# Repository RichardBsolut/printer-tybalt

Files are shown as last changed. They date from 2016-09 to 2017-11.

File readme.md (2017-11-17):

# Tybalt

my version of the [Printer Kitten](https://github.com/woolfepr/Printer-Kitten)

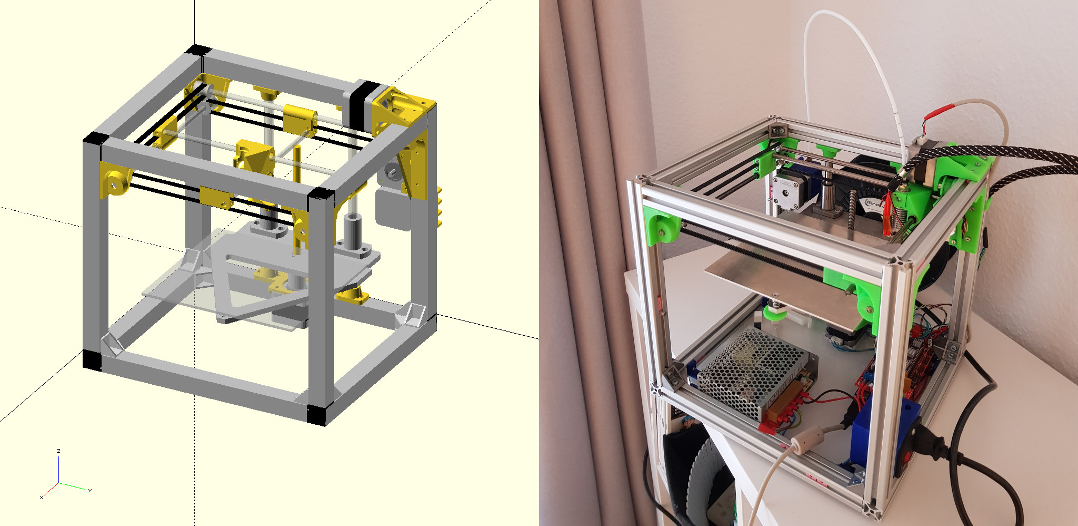
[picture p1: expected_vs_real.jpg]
Expected vs Real


### Why not simple use Kitten ?

Kitten only publishs the stl file, now we have openscad parts.
Mit 34mm schnupfmuffe und vorzerstaeuber druckluft trichter waere sehr schoen.

## Bom

The list is more an  overview not a final list

| Part | Amount | Price | Final Price | Comment
|---|---:|---:|---:|:---|
| Nema 17 | 4 | 2.65 € | 10.60 € | Lucky ebay shot |
| Power Supply 12V-/4,2A | 1 | 14.35 € | 14.35 € | [Pollin](http://www.pollin.de/shop/dt/OTc4ODQ2OTk-/Stromversorgung/Netzgeraete/Festspannungs_Netzgeraete/Schaltnetzteil_MEANWELL_RS_50_12_12_V_4_2_A.html) |
| Power plug | 1 |  6.00 € | 6.00 € | [Amazon](https://www.amazon.de/dp/B00ZCMOIYA) |
| Hot end | 1 | 8.69 € | 8.69 € | [Amazon](https://www.amazon.de/dp/B00V5W00RU) |
| Fan 12V 25x25x10mm | 1 | 3.90 € | 3.90 € | [Reichelt](http://www.reichelt.de/FAN-2510-12V/3/index.html?ACTION=3&LA=446&ARTICLE=11003&artnr=FAN-2510+12V) |
| Ramps + Arduino Mega + Motor Driver | 1 | 15.24 € | 15.24 € | [Aliexpress](https://de.aliexpress.com/item/Mega-2560-R3-1pcs-RAMPS-1-4-Controller-5pcs-A4988-Stepper-Driver-Module-for-3D-Printer/1227994962.html)
| Hallsensor TLE 4905L | 3 | 0.64 € | 1.92 € | [Reichelt](http://www.reichelt.de/TLE-4905L/3/index.html?ARTICLE=25717)
| GT2 Pulley 16  | 2 | 1.00 € | 2.00 € | [Ebay](http://www.ebay.de/itm/181838550531)
| GT2 Pulley 20  | 8 |  | 5.60 € | [Aliexpress](https://www.aliexpress.com/item/Hot-Sale-10pcs-lot-3D-Printer-Parts-Accessory-GT2-20teeth-20-teeth-Timing-Alumium-Pulley-Bore/32323132171.html)
| GT2 Belt  | 3 meter | 1.00 €  | 3.00 € | [Ebay](http://www.ebay.de/itm/161918795821)
| Bearing 626ZZ  | 8 | 0.75 €  | 6.00 € | [Pollin](http://www.pollin.de/shop/dt/ODY1OTU1OTk-/Werkstatt/Eisenwaren/Lager/Kugellager_626ZZ.html)
| Linear shaft D 10mm L 230mm | 2 | 6.61 €  | 13.22 € | [Misumi](http://www.misumi-europe.com/de/e-catalog/vona2/detail/110302634310/)
| Linear Bushing LHICD10 | 2 | 10.98 €  | 21.96 € | [Misumi](http://www.misumi-europe.com/de/catalog/vona2/detail/110300026970/)
| Linear Bushing LMKW6 | 2 | 7.20 €  | 14.40 € | [Misumi](http://www.misumi-europe.com/de/catalog/vona2/detail/110302037730/)
| Stripper Bolt MSB5-20 | 2 | 0.60 €  | 1.20 € | [Misumi](http://www.misumi-europe.com/de/catalog/vona2/detail/110300249140/)
| Lead Screw THSL-200-8D 200m | 1 | 5.87 € | 5.87 € | [Aliexpress](https://de.aliexpress.com/item/3D-Printer-THSL-200-8D-Lead-Screw-Dia-8MM-Pitch-2mm-Lead-4mm-Length-200mm-with/32702416900.html)
| **Frame** |
| 20x20 I-Typ Nut 5 L: 250mm | 10 | 0.73 € | 7.30 € | [motedis](http://www.motedis.com/shop/Nutprofil/20-I-Typ-Nut-5/Aluprofil-20x20-I-Typ-Nut-5::1076.html) |
| 20x20 I-Typ Nut 5 L: 210mm | 2 | 0.62 € | 1.24 € | [motedis](http://www.motedis.com/shop/Nutprofil/20-I-Typ-Nut-5/Aluprofil-20x20-I-Typ-Nut-5::1076.html) |
| Winkel 20 I-Typ Nut 5 | 16 |  | 12.57 € | [motedis](http://www.motedis.com/shop/Nutprofil-Zubehoer/Zubehoer-20-I-Typ-Nut-5/Winkel-20-I-Typ-Nut-5::732.html) |
| M3 Screws | a lot | | |
| **Heated bed** |
| Heated bed 12x12cm 230V 110 Watt | 1 | 25.00 € | 25.00 € | [Ebay](http://www.ebay.de/itm/322240833571) |
| SSR-40DA | 1 |  4.21 € | 4.21 € | [Amazon](https://www.amazon.de/dp/B008OF0PBC) |
| ***Total*** | | | ***184.27 €*** | + unbelievable amount of postage |

## Printed parts
| Part | Time | Length | Gram |
|---|---:|---:|---:|
| **Carraige** |
| Clamps | 25m | 1.62m | 5g |
| Carriage | 1h 55m | 9.19m | 24g |
| **Motor** |
| y | 50m | 4.07m | 12g |
| x | 1h 35m | 7.94m | 24g |
| z | 41m | 3.31m | 10g |
| Beltguide | 1.7m | 1.31m | 4g |
| **Frame** |
| Z Hold | 53m | 3.99m | 12g |
| Z Magenet | 10m | 0.53m | 2g |
| **Printhead** |
| Printhead | 1h 30m | 6.96m | 21g |
||
| ***Total*** | *8h 16m* | *39.31m* | 114g |

*Finally*
http://pr0gramm.com/top/1498986

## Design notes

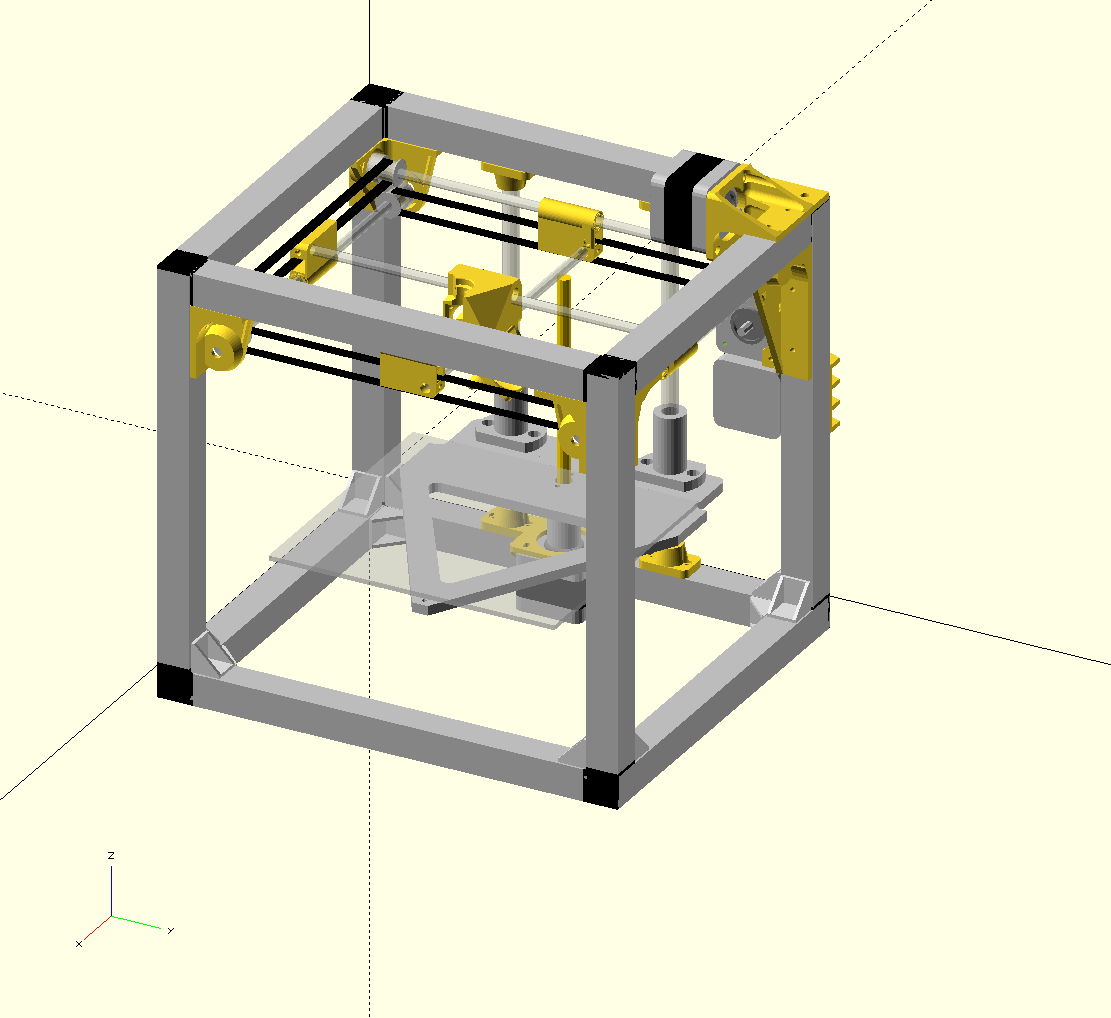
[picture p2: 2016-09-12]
expected.png

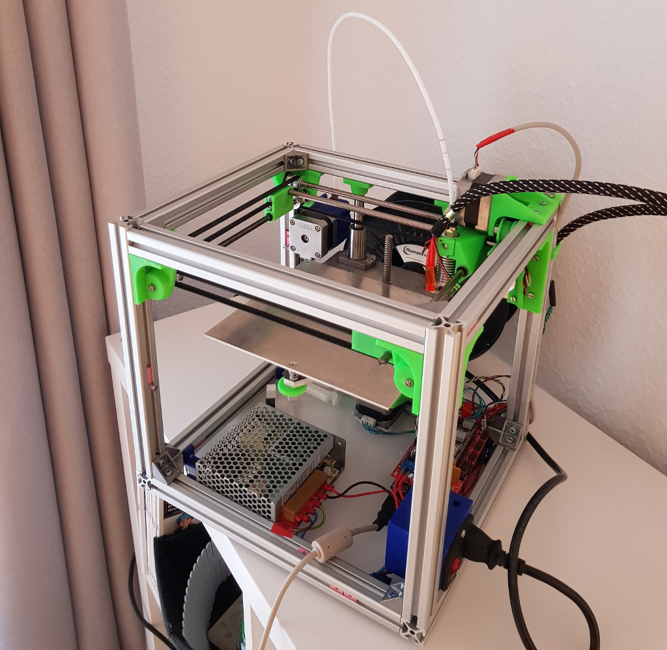
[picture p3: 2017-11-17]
real.jpg

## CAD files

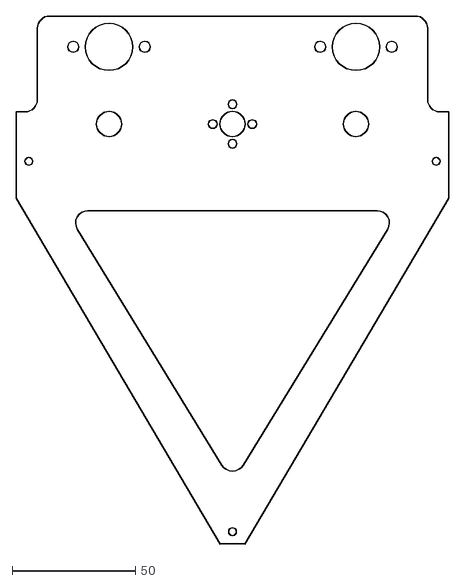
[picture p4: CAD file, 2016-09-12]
dxf/traegerplatte.dxf
175.0 x 213.9

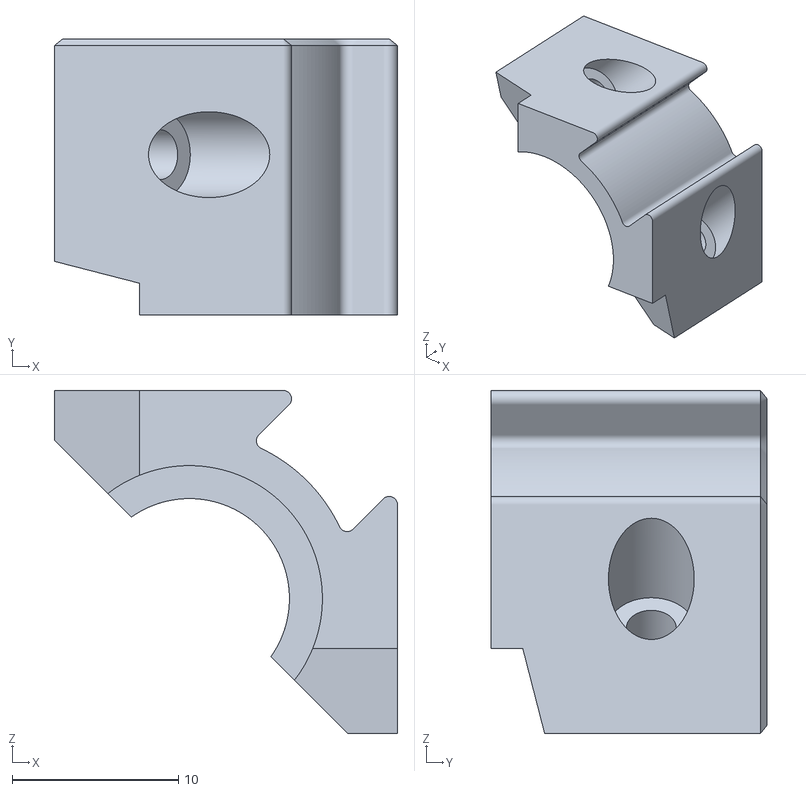
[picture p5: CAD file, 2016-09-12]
kitten_parts/print_head_clamp.stl
20.6 x 16.6 x 20.6

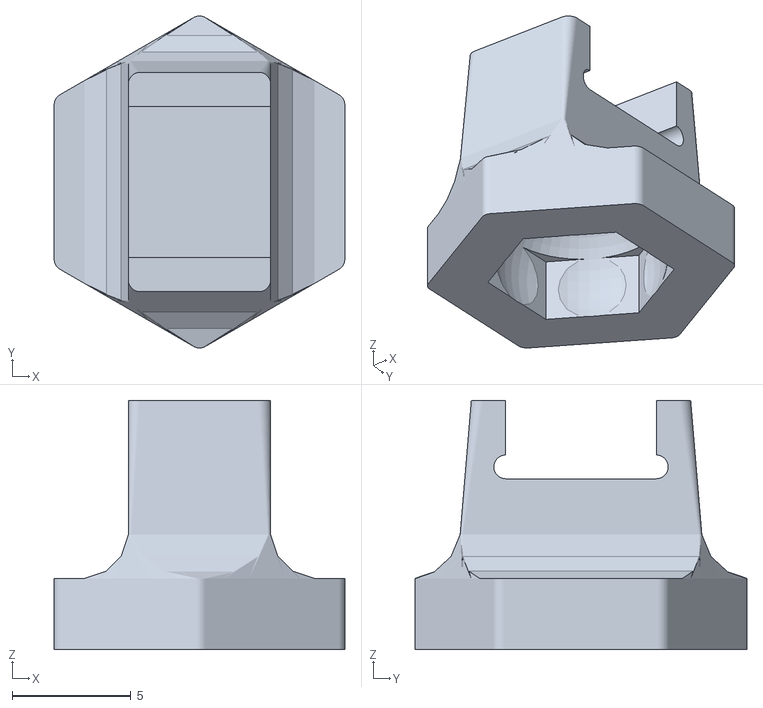
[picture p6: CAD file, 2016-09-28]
output/simple_zprobe.stl
12.3 x 14.0 x 10.5

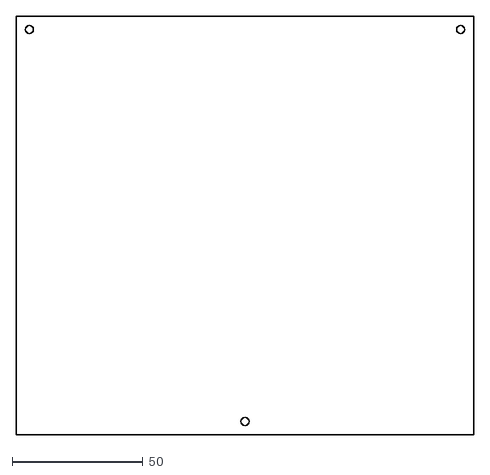
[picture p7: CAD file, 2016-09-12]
dxf/platte.dxf
175.0 x 160.0

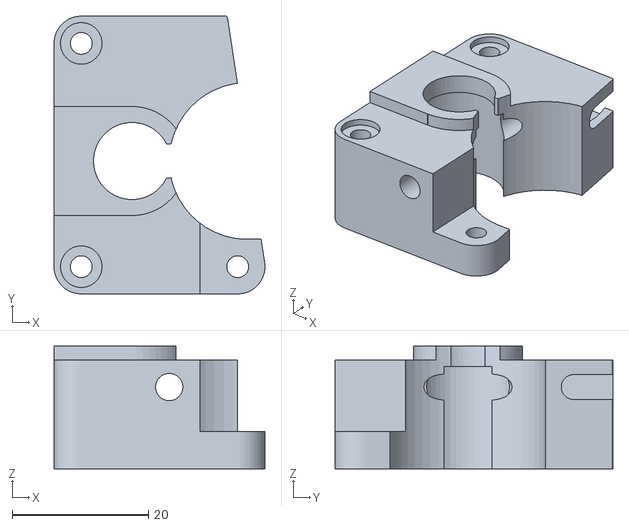
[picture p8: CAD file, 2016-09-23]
output/extruda2_base.stl
30.9 x 40.7 x 18.0

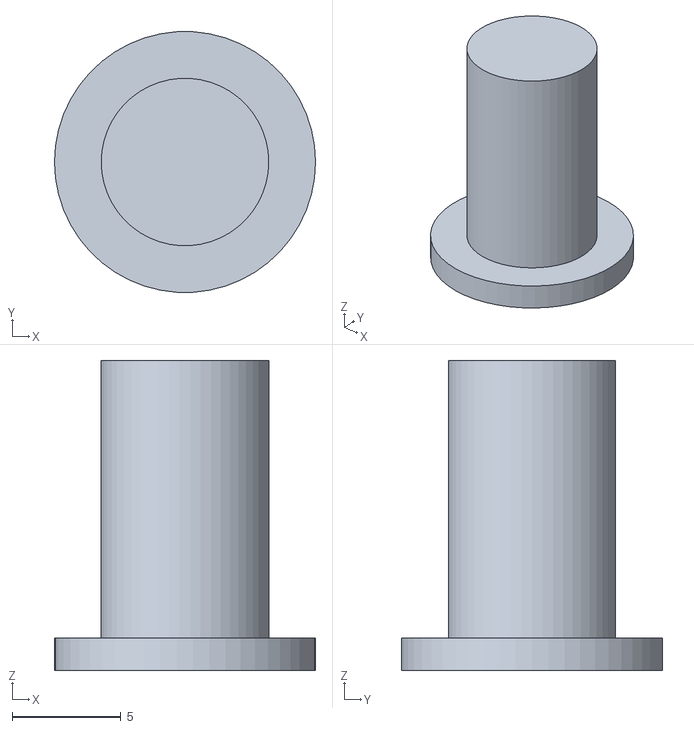
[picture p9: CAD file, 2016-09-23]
output/extruda2_plug.stl
12.0 x 12.0 x 14.2

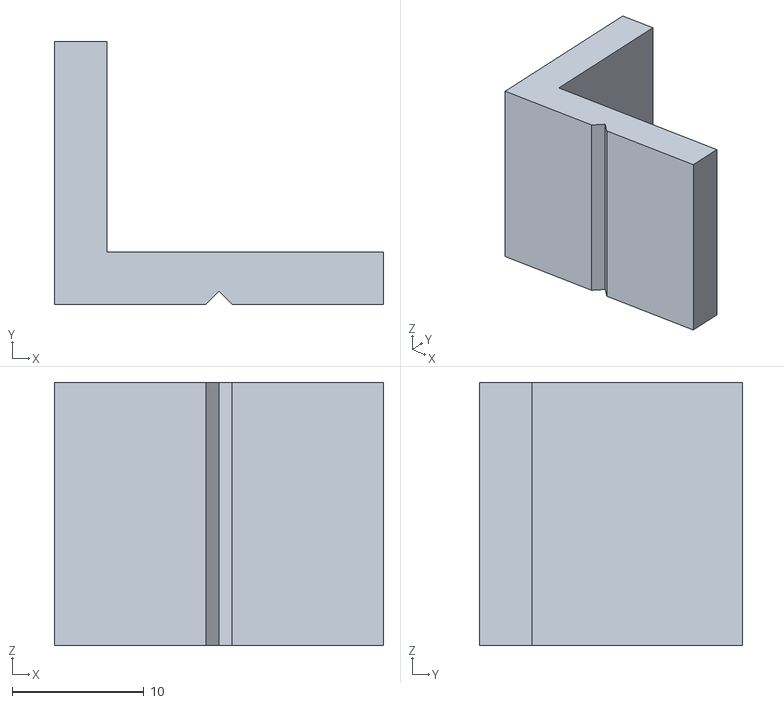
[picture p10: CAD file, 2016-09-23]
output/tools-vicejaw.stl
25.0 x 20.0 x 20.0

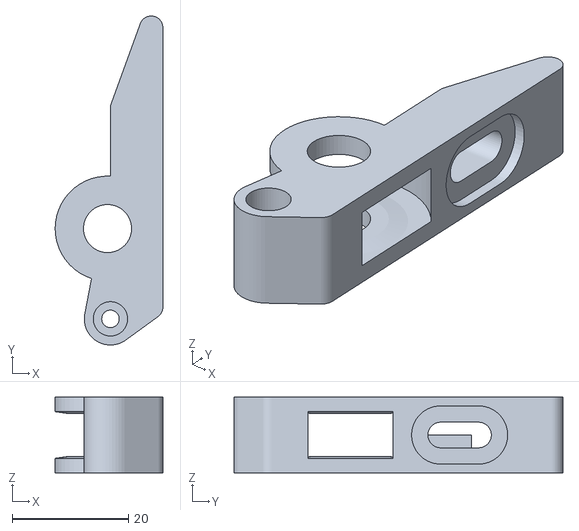
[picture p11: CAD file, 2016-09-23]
output/extruda2_idler.stl
18.5 x 56.5 x 13.0

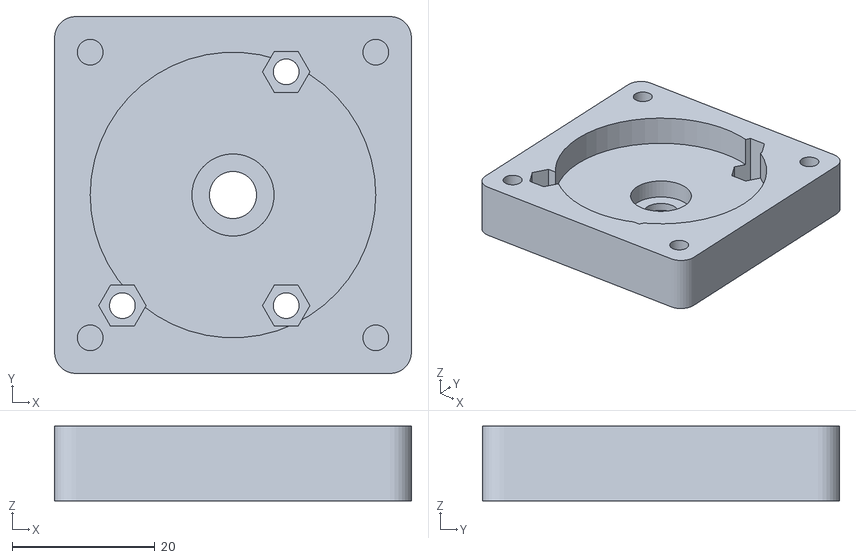
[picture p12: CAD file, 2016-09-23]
output/extruda2_cover.stl
50.0 x 50.0 x 10.5

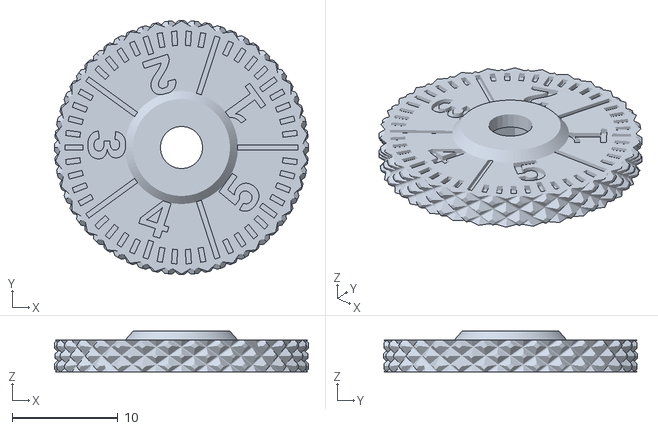
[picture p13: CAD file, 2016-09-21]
output/thumbeheelM3.stl
24.0 x 24.0 x 3.85

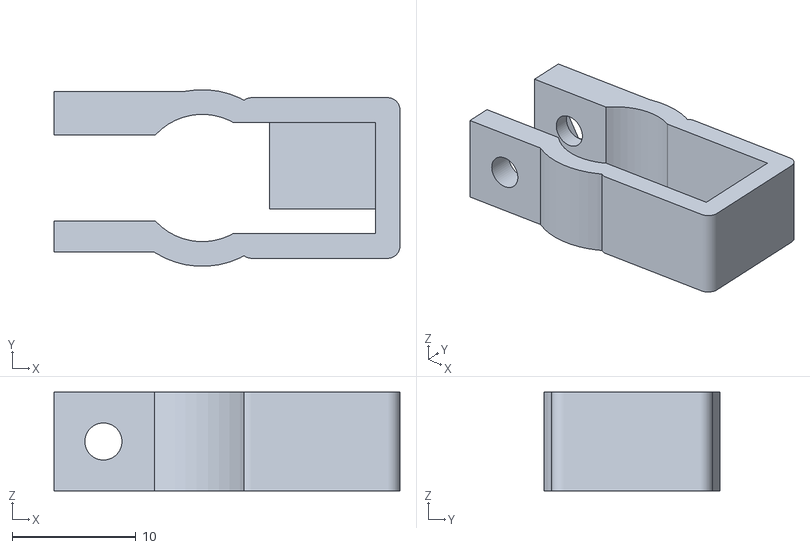
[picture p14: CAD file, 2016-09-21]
output/zendstop2.stl
28.0 x 14.3 x 8.00

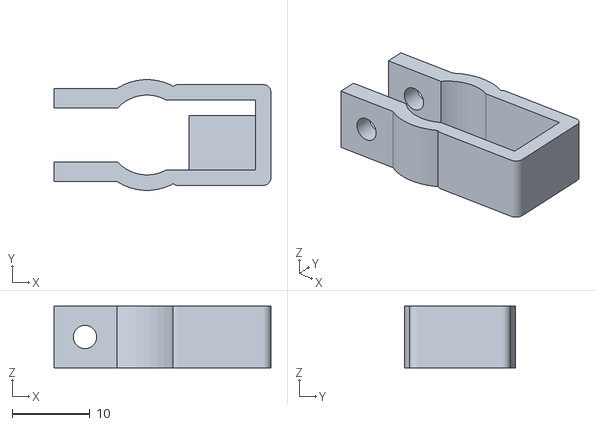
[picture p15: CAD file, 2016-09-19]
output/zendstop.stl
28.0 x 14.3 x 8.00

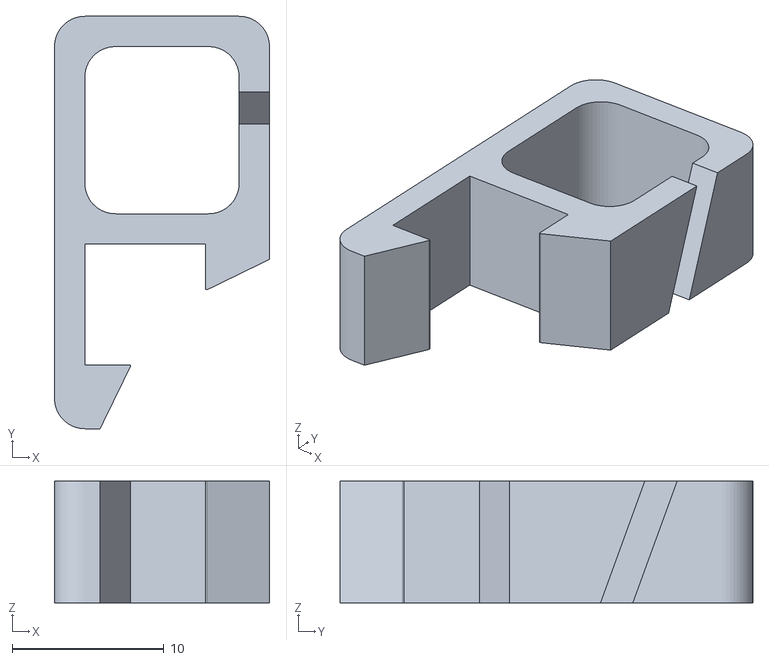
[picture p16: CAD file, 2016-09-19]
output/cable.stl
14.2 x 27.1 x 8.00

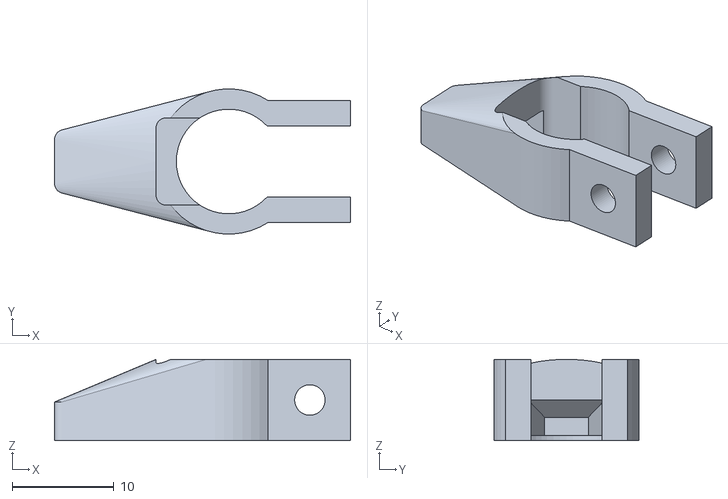
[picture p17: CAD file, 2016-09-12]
output/zsensor.stl
29.1 x 14.3 x 8.00

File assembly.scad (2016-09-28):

use <lib/bcad.scad>
use <lib/screw.scad>
use <lib/motor/17HD.scad>
include <./cfg.scad>
use <./vitamins.scad>

use <../libs/devboard/arduino.scad>;

move(y=-PY/2) 
{
    move(x=PX/2,y=PY/2)
        frameAssembly();    
    move(y=PY,z=PZ)
        xAssembly();    
    move(y=PY,z=PZ-PROFILE)
        topAssembly();
    move(z=-PROFILE)
        printHeadAssembly();

    move(x=PROFILE,y=PY/2,z=0)
    zrot(-90)
        zAssembly();
    
    //Deco
    move(y=PROFILE,x=PROFILE+35,z=-PROFILE)
        color("grey")powerSupply();
 
    move(y=PY-PROFILE-55,x=50,z=-PROFILE)
    move(x=102) zrot(90)
    translate([53.5/2,101.6/2, 0])     
        arduino_mega();
}




move(x=PX-10)
yrot(-30) zrot(90)xrot(90)
move(x=-144/2)
    screenLBL11337();

    
module imp(name) {
    import( str("./output/",name) );
}


module extruder() {
    motorScrewOffset = (motorSize-motorScrewSpacing)/2;
    imp("extruda_holder.stl");
    move(z=-motorH+15) {
        17HD();
        move(z=motorH) {
            move(x=motorSize/2, y=motorSize/2)
                imp("extruda_base.stl");            
            move(x=motorSize-motorScrewOffset,y=motorScrewOffset,z=WALL)
                imp("extruda_idler.stl");
        }
    }
}


module frameAssembly() {  
    //Bottom rails
    yflip_copy()
    move(x=-PX/2, y=-PY/2)
    yrot(90)
        profile(PX);
    
    xflip_copy()
    move(x=-PX/2,y=-PY/2+PROFILE)
    xrot(-90)
        profile(PX);
    
    yflip_copy()
    xflip_copy()
    move(x=-PX/2+PROFILE,y=-PY/2+PROFILE)
    xrot(-90)
    profileCorner();  
    
    //Middle rails
    xflip_copy()
    yflip_copy()
    move(x=-PX/2,y=-PY/2) {
        profile(PX); 
        move(x=PROFILE,y=1)
            profileCorner();  
        move(x=PROFILE-1, y=PROFILE)
        zrot(90)
            profileCorner();  
    }
    
    //top rails
    move(z=PZ) {
        yflip_copy()
        move(x=-PX/2+PROFILE, y=-PY/2)
        yrot(90)
            profile(PX-PROFILE*2); 
        xflip_copy()
        move(x=-PX/2,y=-PY/2+PROFILE)
        xrot(-90)
            profile(PX);   
    }
}

//http://www.motedis.com/shop/Nutprofil-Zubehoer/Zubehoer-20-I-Typ-Nut-5/Winkel-20-I-Typ-Nut-5::732.html
module profileCorner() {
    SHELL= 2;
    color("Gainsboro")
    difference() {
        hull() {
            cube([18,18,SHELL]);
            cube([SHELL,18,18]);
        }
        move(x=SHELL,y=SHELL,z=SHELL)
            cube([18,18-SHELL*2,18]);
    }
}


module xAssembly() {
    move(x=motorSize+PROFILE,y=-motorH-WALL-20-PROFILE_SIZE,z=-motorSize/2)
    zrot(90) {
        imp("yMotorMount.stl");
        move(z=motorSize)
        yrot(90)
            17HD();
    }
}


module topAssembly() {       
    move(x=PROFILE, y=-motorSize-PROFILE,z=-motorSize-(XY_BEARING_MIN_WALL+XY_BEAR_D)*2)
    zrot(90) {
        imp("cornerMotor.stl");
        move(y=motorH+4)
        xrot(90)
            17HD();
    }
    
    move(z=-X_BEAR_POS-XY_SPACE-XY_BEAR_D/2-WALL) {
        move(x=PX-PROFILE,y=-PROFILE)
        zrot(-90)
            imp("corner_2x.stl");
        
        move(x=PROFILE,y=-PY+PROFILE)
        zrot(90)
            imp("corner_2x.stl");
        
        move(x=PX-PROFILE,y=-PY+PROFILE)
        zrot(90)
            imp("corner_flip.stl");
    }
}


module printHeadAssembly() {
    move(x=PROFILE, y=PROFILE+X_BEAR_POS, z=PZ-XY_SPACE-X_BEAR_POS)
        topRods(width=PY-PROFILE*2-X_BEAR_POS*2,length=PX-PROFILE*2);

    move(x=PX-PROFILE*2+X_BEAR_POS,y=PROFILE,z=PZ-X_BEAR_POS)
    zrot(90)
        topRods(width=PX-PROFILE*2-X_BEAR_POS*2,length=PY-PROFILE*2,carriageFilp=true);

    move(x=PX/2,y=PY/2-20, z=PZ-64)
    zrot(90) xrot(90)
        import("./kitten_parts/print_head.stl");
}

module topRods(length=PX-PROFILE*2, width=PY,carriageFilp=false) {
    CARRIAGE_LEN = 35;
    
    move(y=width/2) {   
        yflip_copy()
        move(y=-width/2)
        yrot(90) 
        {
            %cylinder(d=6,h=length);
            gt2pulley();
            move(z=length)
            zflip() gt2pulley();
            
            move(z=(length-CARRIAGE_LEN)/2)
            xrot(90) yrot(carriageFilp ? 0 : 180)
                imp("carriage.stl");
        }
    }
    
    //Belt
    color("black") 
    zflip_copy() {
        move(x=7,z=6) {
            cube([6,width,1]);
            move(x=length-22)
                cube([6,width,1]);
        }
    }
    
    move(y=width/2) {   
        move(y=-width/2)
        yrot(90) 
        {
            move(z=(length-CARRIAGE_LEN)/2)
            xrot(90) yrot(carriageFilp ? 0 : 180)
            move(y=CARRIAGE_LEN-6.8,x=CARRIAGE_ROD_SPACE,z=carriageFilp ? -width : 0)
                %cylinder(d=6,h=width);
        }
    }
    
}


module zAssembly(plate=10){    
    move(x=-(motorSize+6)/2,y=0, z=-PROFILE+WALL)
        imp("zmotorhold.stl");
    
    move(y=motorSize/2, z=motorH-PROFILE) {
        17HD(center=true);
        up(3) {
            coupler();
            color("gold") cylinder(d=8,h=165);
        }
    }    
    
    xflip_copy()
    move(x=50,y=-10) {
        imp("zhold.stl");
        %cylinder(d=10,h=PZ-PROFILE);        
        move(z=PZ-PROFILE)
            zflip() imp("zhold.stl");    
    }

    move(z=6+50+plate) {
        color("silver")
        move(z=-6,y=21.25)
            yflip()linear_extrude(height=6)
                import("./dxf/traegerplatte.dxf");
        
        //Print space
        %move(x=-180/2, y=21.25+10,z=10)
            cube([180,170,3]);
        
        color("silver")
        xflip_copy()
            move(x=50,y=-PROFILE/2) {
                LHICD10();   
                
                xflip_copy()
                move(x=29/2,z=-10)
                    cylinder(d=4,h=10);
            }
    }

    move(x=-50,y=-10,z=40)
        zflip() imp("zsensor.stl");    
}

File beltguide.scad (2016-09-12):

use <./lib/bcad.scad>
include <./cfg.scad>

beltGuide();

module betlGuideRamp(d) {
    cylinder(d=d+2,d2=d+3, h=0.5);
    up(0.5) cylinder(d=d+3, h=1);
    up(1.5) cylinder(d=d+3,d2=d+.1, h=1);    
}

module beltGuide(d=18.5, noBearing=false) {
    difference() {
        union() {
            betlGuideRamp(d);
            up(2.5) cylinder(d=d,h=12-2.5-2.5);
            up(12) zflip() betlGuideRamp(d);
        }
        down(1)
            cylinder(d=11+0.3,h=20);
    }    
}

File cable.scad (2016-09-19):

use <./lib/bcad.scad>
include <./cfg.scad>
use <./vitamins.scad>

PLAY = 0.1;
hookLen = PROFILE_CUT + (PROFILE_SIZE-PROFILE_CUT)/2;
WALL=2;
$fn=50;

fullClip(h=8,intersect=1,deep=3);
    
module fullClip(h=8,width=15,r=2,gap=2,gapDeg=20,deep=2.1,intersect=0.8) {
    holder(h=h,r=r,intersect=intersect,deep=deep);
    clip(width=width,h=h,gap=gap,gapDeg=gapDeg);
}

    
module holder(intersect=0.8,deep = 2.1, h=8,r=2) {
    cube([hookLen+WALL,WALL,h]);
    translate([WALL,-hookLen,0]) {
        hull() {
            move(y=PROFILE_CUT-0.1-PLAY)
                cube([deep,0.1,h]);
            cube([intersect,0.1,h]);
        }

        move(x=hookLen,y=hookLen)
        zrot(90)
        xflip()
        hull() {
            move(y=PROFILE_CUT-0.1-PLAY)
                cube([deep,0.1,h]);
            cube([intersect,0.1,h]);
        }
        difference() {
            move(x=-WALL)
                rrect([hookLen+WALL,hookLen+WALL,h],r=r);
            move(y=-1,z=-1)
                cube([hookLen+1,hookLen+1,h+2]);
        }
    }
}    

module clip(width=10,h=8,gap=WALL,gapDeg=30) {
    difference() {
        rrect([hookLen+WALL,width,h],r=2);
        move(x=WALL,y=WALL,z=-1)
            rrect([hookLen-WALL,width-WALL*2,h+2],r=2);    
        
        move(x=hookLen+5,y=(width)/2,z=h/2)
        xrot(-gapDeg)
            cube([20,gap,h*4],center=true);
    }
}

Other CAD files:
output/printhead.stl
output/zhold.stl
output/zmotorhold.stl
output/beltguid.stl
carriage.scad
cfg.scad
extruda.scad
frame.scad
output/carriage_clamps.stl
output/carriage_test.stl
output/clamp_test.stl
output/cornerMotor.stl
output/corner_2x.stl
output/corner_flip.stl
output/cring.stl
output/sandpaperholder.stl
output/yMotorMount.stl
output/zmagnethold.stl
printhead.scad
tools.scad
vitamins.scad
z.scad

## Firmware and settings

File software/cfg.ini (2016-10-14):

[profile]
layer_height = 0.25
wall_thickness = 0.4
retraction_enable = True
solid_layer_thickness = 0.25
fill_density = 20
print_speed = 50
print_temperature = 210
print_temperature2 = 0
print_temperature3 = 0
print_temperature4 = 0
print_temperature5 = 0
print_bed_temperature = 0
support = None
platform_adhesion = None
support_dual_extrusion = Both
wipe_tower = False
wipe_tower_volume = 15
ooze_shield = False
filament_diameter = 1.75
filament_diameter2 = 0
filament_diameter3 = 0
filament_diameter4 = 0
filament_diameter5 = 0
filament_flow = 100.0
nozzle_size = 0.4
retraction_speed = 100.0
retraction_amount = 10
retraction_dual_amount = 16.5
retraction_min_travel = 1.5
retraction_combing = All
retraction_minimal_extrusion = 0.02
retraction_hop = 0.3
bottom_thickness = 0.24
layer0_width_factor = 100
object_sink = 0.0
overlap_dual = 0.15
travel_speed = 100.0
bottom_layer_speed = 10
infill_speed = 0.0
solidarea_speed = 0.0
inset0_speed = 0.0
insetx_speed = 0.0
cool_min_layer_time = 15
fan_enabled = True
skirt_line_count = 0
skirt_gap = 3.0
skirt_minimal_length = 100.0
fan_full_height = 3
fan_speed = 100
fan_speed_max = 100
cool_min_feedrate = 10
cool_head_lift = False
solid_top = True
solid_bottom = True
fill_overlap = 15
perimeter_before_infill = False
support_type = Grid
support_angle = 60
support_fill_rate = 15
support_xy_distance = .7
support_z_distance = 0.15
spiralize = False
simple_mode = False
brim_line_count = 20
raft_margin = 5.0
raft_line_spacing = 3.0
raft_base_thickness = 0.3
raft_base_linewidth = 1.0
raft_interface_thickness = 0.27
raft_interface_linewidth = 0.4
raft_airgap_all = 0.0
raft_airgap = 0.22
raft_surface_layers = 2
raft_surface_thickness = 0.27
raft_surface_linewidth = 0.4
fix_horrible_union_all_type_a = True
fix_horrible_union_all_type_b = False
fix_horrible_use_open_bits = False
fix_horrible_extensive_stitching = False
plugin_config = 
object_center_x = -1
object_center_y = -1

[alterations]
start.gcode = ;Sliced at: {day} {date} {time}
	;Basic settings: Layer height: {layer_height} Walls: {wall_thickness} Fill: {fill_density}
	;Print time: {print_time}
	;Filament used: {filament_amount}m {filament_weight}g
	;Filament cost: {filament_cost}
	;M190 S{print_bed_temperature} ;Uncomment to add your own bed temperature line
	;M109 S{print_temperature} ;Uncomment to add your own temperature line
	;G21        ;metric values
	;G90        ;absolute positioning
	;M82        ;set extruder to absolute mode
	;M107       ;start with the fan off
	;G28 X0 Y0  ;move X/Y to min endstops
	;G28 Z0     ;move Z to min endstops
	;G1 Z1.0 F{travel_speed} ;move the platform down 1mm
	;G92 E0                  ;zero the extruded length
	;G1 F200 E10              ;extrude 3mm of feed stock
	;G1 Z10.0 F{travel_speed} ;move the platform down 9mm
	;G92 E0                  ;zero the extruded length again
	;G1 F{travel_speed}
	;Put printing message on LCD screen
	;M117 Printing...

        G21              ;metric values
        G90              ;absolute positioning
        M82              ;set extruder to absolute mode
	M107             ;start with the fan off
	G28 X0 Y0        ;move X/Y to min endstops
	G28 Z0           ;move Z to min endstops

        G1 Z5            ;z down
	M140 S{print_bed_temperature}
	M104 S{print_temperature}
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

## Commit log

2016-09-12 Added extra height for zmotorhold
    [z.scad]
2016-09-12 New extra height
    [z.scad]
2016-09-12 Add profile sizes to cfg
    [cfg.scad]
2016-09-12 First cable clamp
    [cable.scad, cable.stl]
2016-09-19 Clean cable holder
    [cable.scad]
2016-09-19 New/old style zendstop
    [vitamins.scad, z.scad, zendstop.stl]
2016-09-21 Fix carraige rod space
    [cfg.scad]
2016-09-21 New style for z endstop
    [z.scad, zendstop2.stl]
2016-09-21 Try to add a dial indicator
    [tools.scad]
2016-09-21 Added cable clip holes for printhead
    [printhead.scad, printhead.stl]
2016-09-21 Use thumbwheel for z springs
    [thumbeheelM3.stl, thumbwheelM3.scad]
2016-09-23 New assembly style
    [assembly.scad, extruda2_base.stl, extruda2_cover.stl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]
2016-09-23 Added MR115 bearing
2016-09-23 Simple Vice jaws
    [tools.scad]
2016-09-23 More screw hole play
    [vitamins.scad]
2016-09-23 New planetary gear extruder
    [extruda2.scad, extruda_base.stl, extruda_holder.stl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]
2016-09-23 Clean extruder code
    [extruda2.scad, vitamins.scad]
2016-09-23 Moved thumbwheel to tools
    [thumbwheelM3.scad, tools.scad]
2016-09-23 Clean up assembly
    [assembly.scad]
2016-09-23 Added new screen type
    [vitamins.scad]
2016-09-28 Added screen LBL11337
    [assembly.scad]
2016-09-28 Added an simple zprobe
    [simple_zprobe.stl, tools.scad]
2016-10-14 Least updates
    [extruda2.scad, tools.scad, vitamins.scad]
